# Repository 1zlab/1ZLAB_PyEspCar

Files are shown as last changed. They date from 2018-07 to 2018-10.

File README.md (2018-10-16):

# PyEspCar - 基于MicroPython-ESP32的WIFI小车

**1Z实验室出品**
**1ZLAB**： **Make Things Easy**

## 项目简介

1ZLab在准备挑选合适的小车来研发计算机视觉的教程时候 , 发现习惯了Python语法的我们, 在市面上找不到合适小车, 后来我们选了ESP32作为小车的控制主板, 可以使用Python对其进行交互式编程, 极大的提升了开发效率.

下图是我们的**PyESPCar V2.1**版本的实物图, 舵机云台上面挂载了手机, 可以通过手机WIFI传图, 然后在PC上用OpenCV做图像处理, 然后PC发送控制指令给PyESPCar WIFI小车. 

## 购买PyESPCar

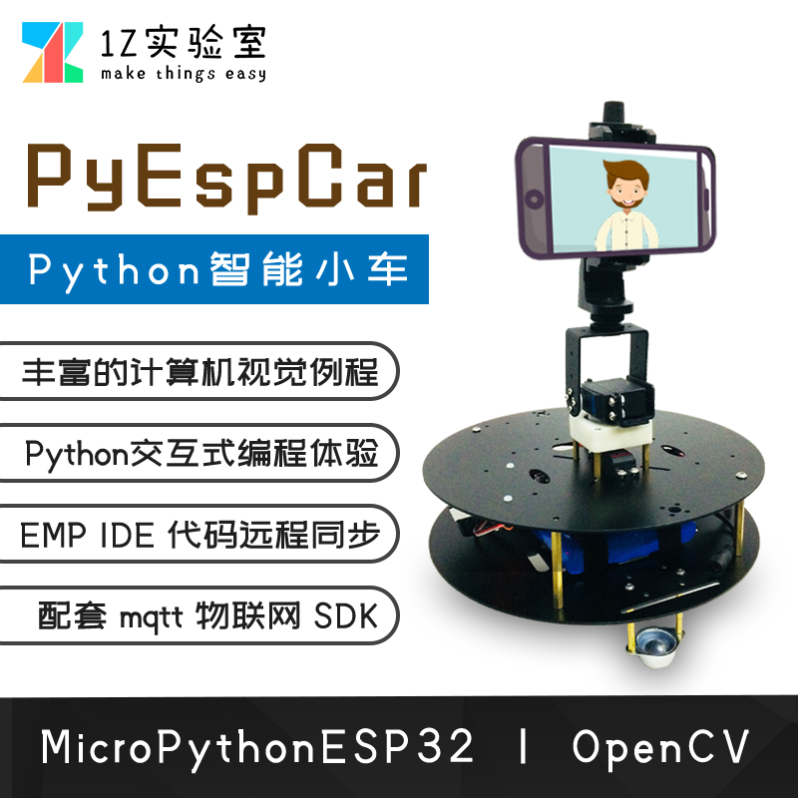
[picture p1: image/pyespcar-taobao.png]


[淘宝-PyESPCar购买链接](https://item.taobao.com/item.htm?id=579247648473)

## 小车自身特性

* MicroPython编程，小车通过repl交互式编程

* **远程调试**，通过WebREPL，可以远程给小车进行编程，上传/同步代码文件。

* 软件硬件与机械结构全部**开源(Open Source)**。

  不用购买之后再提供，直接放在Github上，后续再配套教程持续制作用户友好的**文档**

* **配套教程**  制作PyEspCar Z1的视频教程（讲micropython-esp32与运动控制），发布在**Bilibili**上面， 内容可以参考下文的 `MicroPython-ESP32教学`与 `自控与运动学控制` 这两部分。

  B站主页： https://space.bilibili.com/40344504/#/

* **代码规范**，逐行注释，容易看懂， 参见代码仓库。

* 自主研发**ESP32 Web IDE**， [IDE地址](http://dev.1zlab.com)

## 开发文档

* [PyESPCar开发环境配置](./doc/PyESPCar%E5%BC%80%E5%8F%91%E7%8E%AF%E5%A2%83%E9%85%8D%E7%BD%AE_pyespcar-environment-config/PyESPCar%E5%BC%80%E5%8F%91%E7%8E%AF%E5%A2%83%E9%85%8D%E7%BD%AE_pyespcar-environment-config.md)
## 综合例程

[PyESPCar按键控制模式](https://github.com/1zlab/1ZLAB_PyEspCar/tree/master/examples/01-keyboards_ctl_mode)

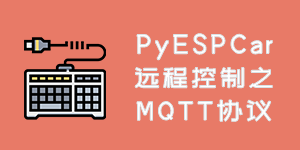
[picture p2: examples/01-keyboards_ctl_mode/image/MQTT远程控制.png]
mqtt keyboards


[PyESPCar色块追踪](https://github.com/1zlab/1ZLAB_PyEspCar/tree/master/examples/02-color-block-track)

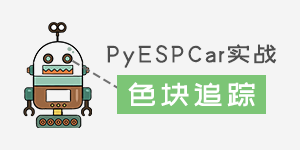
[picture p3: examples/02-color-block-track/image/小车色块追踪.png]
color track


## 机械结构与硬件

* **轻量级二自由度云台**

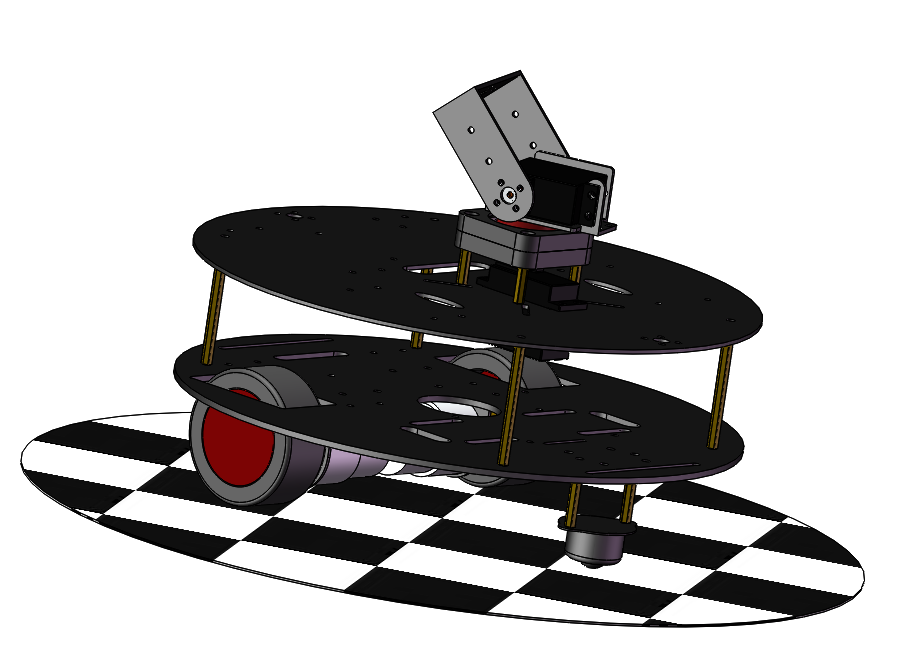
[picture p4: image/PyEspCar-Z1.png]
machine
  

  更适合放在小车上面，同时末端可以承受较大负载（例如手机）。

  高品质20KG 数字舵机， 后期可以拓展为机械臂。

* **PyESPCar 小车底板** 

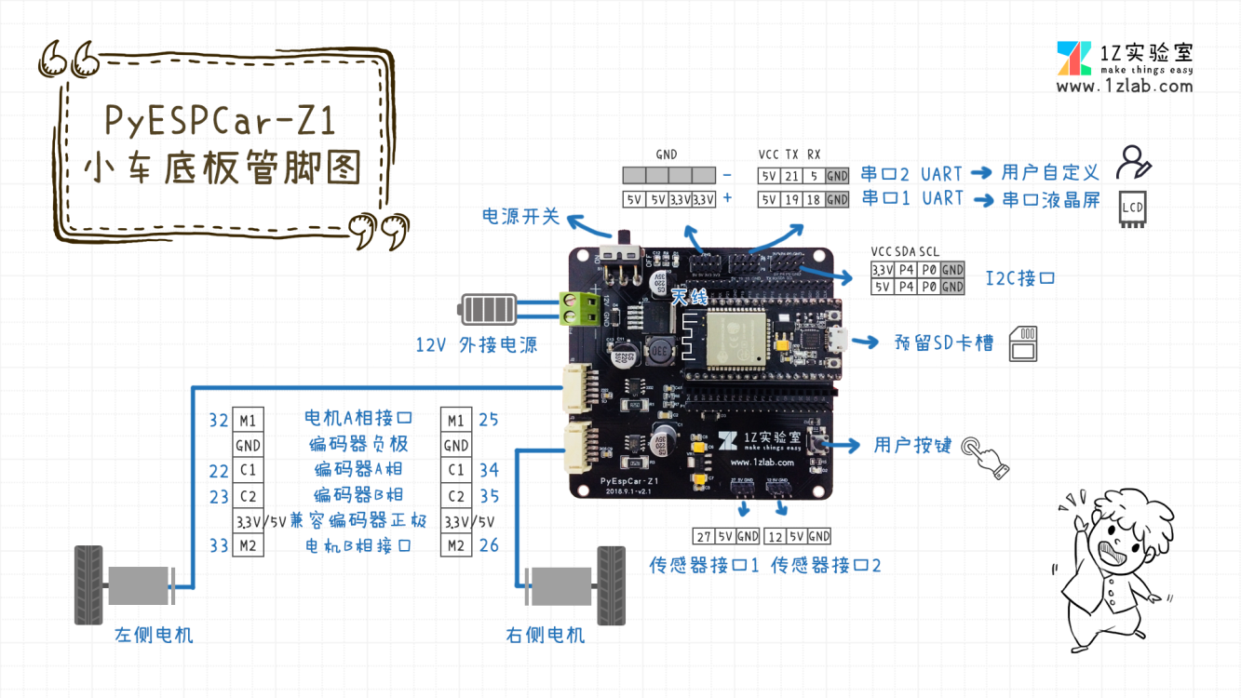
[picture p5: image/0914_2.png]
  

  填补了目前ESP32小车底板的空白，主控采用安信可公司的NodeMCU32s，直插在小车底板上。

  板子预留资源如下: 

  *  用户按键 ×1
  *  电机与AB相编码器接口 ×2
   *  传感器接口×2  
   *  UART串口x2  
   *  I2C接口 x1（两个I2C插口）

* **全金属双层小车底板**  材质选用铝合金，比亚克力更坚固， 尺寸比一般的两轮差速小车大270mm。

  底板上面也预留了**数莓派**，二自由度云台，电池，超声波，ESP32小车控制板,还有**激光雷达**的孔位。

* **12V电池组，电池容量6000毫安时**， 配套充电器

## 贡献者(Ccontributor)

**特别感谢魏彦峰同学在机械结构设计还有小车控制板设计做出的贡献。**

* [魏彦峰-1Z实验室&中国地质大学（武汉）](https://github.com/rose-w)
* [邢顺凯-1Z实验室&杭州电子科技大学](https://github.com/mushroom-x)
* [吴彬聪-1Z实验室&杭州电子科技大学](https://github.com/littleoniononion)
* [刘新宇-廊坊师范](https://github.com/LiuXinyu12378)
* [杨子豪-平衡小车之家](http://minibalance.com/)

## 加入1Z实验室

出品：1Z实验室 （1ZLAB： Make Things Easy）

1Z实验室 Make Things Easy . 致力于在机器人+计算机视觉+人工智能的重叠区域, 制作小白友好的教程.
1zlab

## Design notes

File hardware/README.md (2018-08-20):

# ESP32小车硬件开源文件

## ESP32小车控制板

> TODO 焊接完成之后贴图

## 小车底盘机械结构

>注:所有建模均使用 SolidWorks2016 创建.

* [车身部分](#车身部分)
* [动力部分](#动力部分)
* [云台部分](#云台部分)

### 车身部分

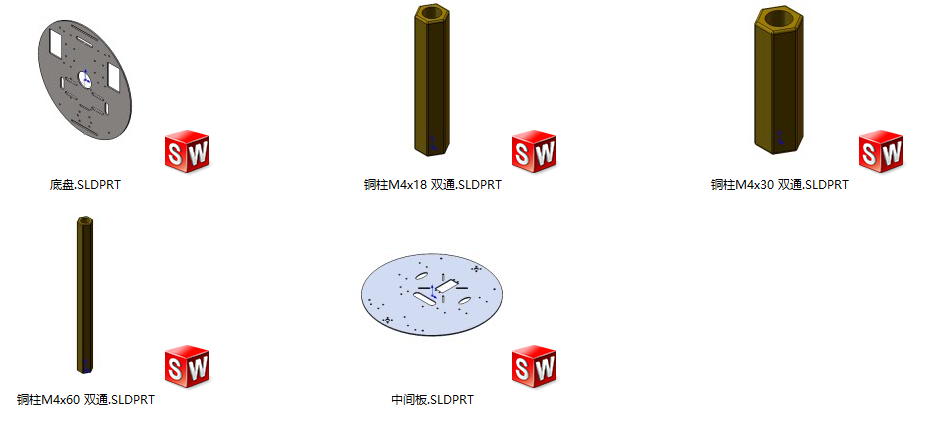
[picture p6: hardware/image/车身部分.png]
车身部分


底盘金属加工图纸

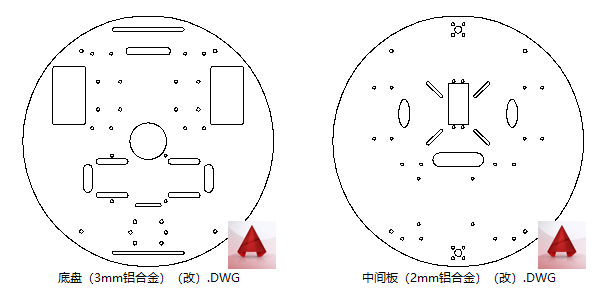
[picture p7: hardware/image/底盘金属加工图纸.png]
底盘金属加工图纸


### 动力部分

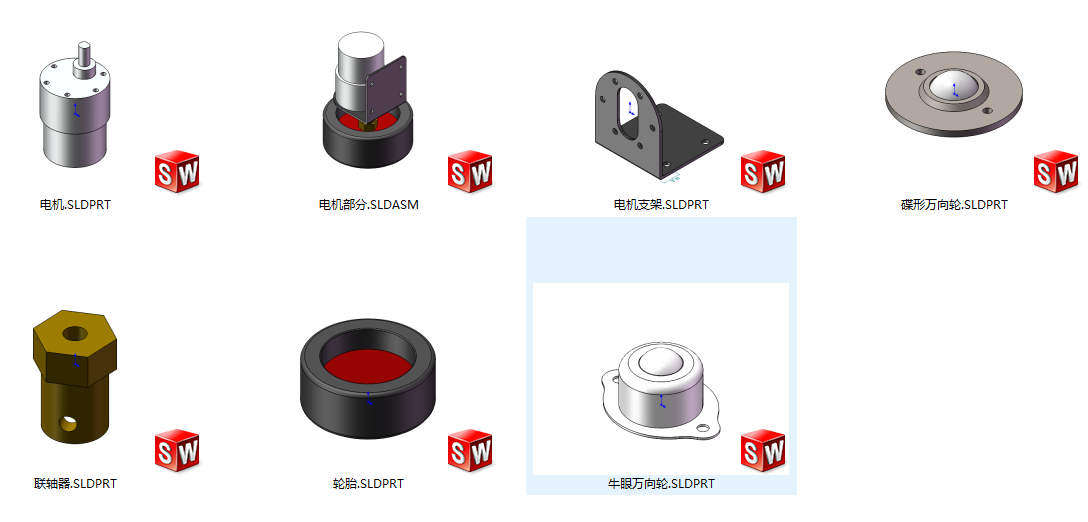
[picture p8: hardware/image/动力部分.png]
动力部分


### 云台部分

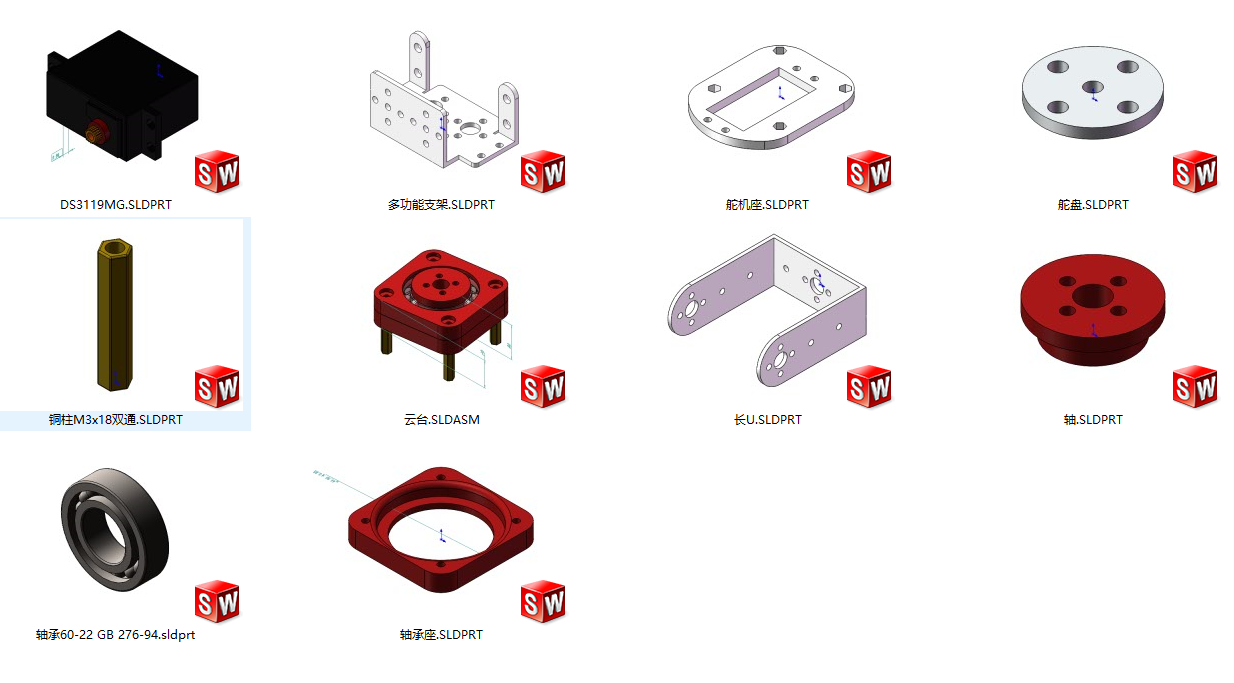
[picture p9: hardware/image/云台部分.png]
云台部分


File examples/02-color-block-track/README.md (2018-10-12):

# PyESPCar色块追踪

## 简介

pyespcar tracker

使用PyESPCar还有OpenCV实现色块追踪, OpenCV识别色块,然后计算偏移量,通过MQTT协议发送给PyESPCar小车. 源码见:https://github.com/1zlab/1ZLAB_PyEspCar/tree/master/examples/02-color-block-track

## 效果演示

效果视频已上传至B站:

[PyESPCar色块追踪效果演示-1Z实验室](https://www.bilibili.com/video/av33370828)

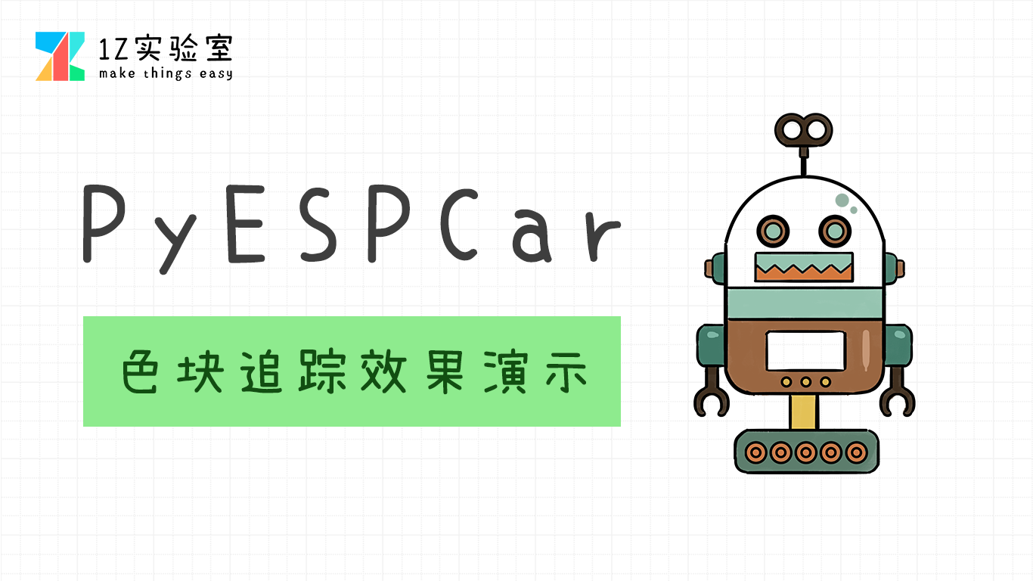
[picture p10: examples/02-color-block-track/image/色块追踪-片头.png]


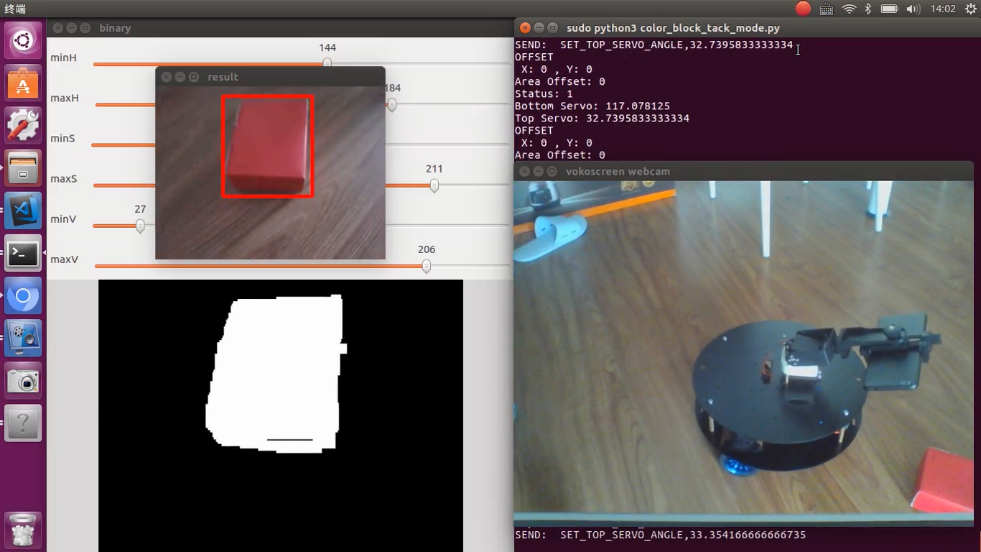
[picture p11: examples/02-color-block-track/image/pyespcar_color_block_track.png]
color block


使用教程与操作流程见`src/README.md`

教程已上传至1zlab.com
[PyESPCar色块追踪小车-主题课程](http://www.1zlab.com/book/opencv-color-track-car-pyespcar/)

加群参与讨论
ad

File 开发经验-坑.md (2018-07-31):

# 存在问题

## 关于ADC的问题

- Invalid Pin for ADC
TODO 查阅文档 需要修改固件 (成本比较高, 而且浪费资源)
IO2 -> ADC2 Channel 2
TODO 改固件 从而可以支持ADC2
临时方案 底板Uno(A0) - 接Uno(A2) = ESP32 GPIO35
BUG 电压取值adc采样 不稳 一直在浮动 

多次采样然后平均
与标准电压比对 (5v 3v) * 系数

## [已解决] IRQ外部中断

MicroPython-ESP32中, irq 只有上升沿或下降沿 (二选1)

>TODO 修改固件, 添加Change模式. 

**而且这里需要的应该是-非阻塞(no-blocking)模式**

**查看ESP-IDF是否有这个API**
是否有必要使用外部中断, 可以使用定时器, 定时查看IO电平是否变化
https://github.com/BramRausch/encoderLib

ESP32 是否有硬件计数?

## [已解决]增量式编码器使用
编码器噪声问题 不是完全按照 0132的顺序来的。

两个引脚都是中断。

TODO 寻找项目参考
添加滤波器

1. 比对 可以大于等于两个？
2. 二者相等的情景？ 
3. 添加状态机 State (之前一直在正转 马上反转的可能性不大。)
4. 是否引入变量： 触发中断的管脚

**增量式编码器**
https://blog.csdn.net/cuhkljt/article/details/25845217
https://item.taobao.com/item.htm?spm=a230r.1.14.27.63de2886VbW8iL&id=45347924687&ns=1&abbucket=6#detail

**ESP32的IRQ是软件中断，相应速度不够， 改用定时器问题就解决了**

## 刷固件

刷固件， 需要把ESP32开发板从底板下取下。
> 有时需要有时不需要

## 声明引脚输入输出是个好习惯
Pin.IN
Pin.OUT

## [Done]电机引脚问题

Problem 左侧电机一动，reboot -> 更换引脚已解决 （因为用了D2接口）

## [Done]电机只能反转不能正转？
电机驱动模块插反
**电机驱动模块有正反**

## Flash损坏，不稳定

ERRORS
----main.py文件损毁？---
rst:0x1 (POWERON_RESET),boot:0x33 (SPI_FAST_FLASH_BOOT)
flash read err, 1000
ets_main.c 371 
ets Jun  8 2016 00:22:57

## [Done 1/2]定时器中断-连不上 传不了文件

main.py里面设定了定时器中断，导致不能通过ampy传文件，只能重置固件。

**ESP32的固件存放在RAM， 文件系统放置在ROM里面, 也就是说，重新刷固件并不会修改文件系统中的代码。**

如果程序里面一直在循环while True，repl资源一直被占用，无法写入程序。
所以需要链接repl，然后将main.py写为空，reboot一下，就解决了。

```python
f = open('main.py', 'w')
f.write('')
f.save
```

在`main.py`里面如果是定时器，定时器一直Print， 这个是个 **死结**
> 这种情况要如何处理？

这个问题可以预防，设置一个外部按键, 然后将main.py清空  write('')
> 修改固件 修改boot.py (留一手)

## 重置MicroPython-ESP32的文件系统

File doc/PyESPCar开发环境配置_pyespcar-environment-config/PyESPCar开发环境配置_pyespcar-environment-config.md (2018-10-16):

# PyESPCar开发环境配置

## 写在前面

自己配置Ubuntu开发环境略麻烦, 后续1Z实验室会提供配置好的虚拟机给大家.

## 为什么用Ubuntu?

我们的PyESPCar开发教程以及OpenCV图像处理部分的教程都是在Ubuntu下进行的, 因为Ubuntu下开发环境更加友好.  同时针对**VIP**用户, 我们还提供Ubuntu远程协助的服务.

Ubuntu是你步入开源世界的大门. 你可以选择在虚拟机下安装Ubuntu, 也可以选择在真机上安装Ubuntu.

在Ubuntu下,  我们的工程使用Python一统天下, Python完成嵌入式开发,机器人控制, Python进行图像处理, Python进行物联网通信. 所以你只需要精通这一门语言就足够了.

## Ubuntu下的开发环境配置

为了大家方便, 这里我还是把Ubuntu所需配置的环境在这里讲一下, 做一下汇总.

### Ubuntu虚拟机安装

如果你是用的Ubuntu虚拟机的话, 1Z实验室有虚拟机的安装教程:

[Ubuntu虚拟机安装-VirtualBox](https://github.com/1zlab/1ZLAB_OpenCV_Tutorial/blob/master/%E9%99%84%E5%BD%95A.OpenCV%E5%BC%80%E5%8F%91%E7%8E%AF%E5%A2%83%E9%85%8D%E7%BD%AE/Ubuntu/1.Ubuntu%E8%99%9A%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)

### Git

git是工程版本管理工具, 你可以使用Git从Github克隆PyESPCar的开源工程.

在Ubuntu上安装git:

```bash
sudo apt-get install git
```

### pip3

Ubuntu16.04自带的默认Python版本是python3.5, 需要安装`pip3` 作为python的包管理工具. 

```bash
sudo apt-get install python3-pip
```

### Python科学计算工具包

做科学计算需要安装下面的一些工具包

```bash
sudo pip3 install jupyter ipython numpy scipy matplotlib
```

### 安装OpenCV

非官方的OpenCV预编译的包.
同时安装opencv的main还有contrib部分.

```bash
pip install opencv-contrib-python
```

详情见文档:
[opencv-python 3.4.3.18](https://pypi.org/project/opencv-python/)

### PyGame

PyGame是用于写游戏的.

因为我们用到了PyGame的键盘事件监听, 所以需要安装这个包.

```bash
sudo pip3 install pygame
```

### MicroPython-ESP32开发环境配置

PyESPCar是基于MicroPython-ESP32的, 所以MicroPython-ESP32的基本操作, 是需要你自己去学习的.

完整的教程见1Z实验室出品的: [MicroPython-ESP32从入门到差不多](https://github.com/1zlab/1ZLAB_MicroPython_ESP32_Tutorial)

下面的教程是你玩PyESPCar必须要看的.

- [MicroPython-ESP32固件烧录](https://github.com/1zlab/1ZLAB_MicroPython_ESP32_Tutorial/blob/master/01_MicroPython-ESP32%E5%9B%BA%E4%BB%B6%E7%83%A7%E5%BD%95/MicroPython-ESP32%E5%9B%BA%E4%BB%B6%E7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)
- [ESP32的REPL使用方法](https://github.com/1zlab/1ZLAB_MicroPython_ESP32_Tutorial/blob/master/02_ESP32%E7%9A%84REPL%E4%BD%BF%E7%94%A8%E6%96%B9%E6%B3%95/ESP32%E7%9A%84REPL%E4%BD%BF%E7%94%A8%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)
- [ESP32接入WIFI热点](https://github.com/1zlab/1ZLAB_MicroPython_ESP32_Tutorial/blob/master/17_ESP32%E6%8E%A5%E5%85%A5WIFI%E7%83%AD%E7%82%B9/ESP32%E6%8E%A5%E5%85%A5WIFI%E7%83%AD%E7%82%B9.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)
- [使用upip安装包](https://github.com/1zlab/1ZLAB_MicroPython_ESP32_Tutorial/blob/master/16_%E4%BD%BF%E7%94%A8upip%E5%AE%89%E8%A3%85%E5%8C%85/%E4%BD%BF%E7%94%A8upip%E5%AE%89%E8%A3%85%E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)
- [WebREPL与MIcroIDE配置教程](https://github.com/1zlab/1ZLAB_MicroPython_ESP32_Tutorial/blob/master/14_WebREPL%E4%B8%8EMIcroIDE%E9%85%8D%E7%BD%AE%E6%95%99%E7%A8%8B/WebREPL%E4%B8%8EMIcroIDE%E9%85%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)
- [利用AMPY进行文件同步](https://github.com/1zlab/1ZLAB_MicroPython_ESP32_Tutorial/blob/master/18_%E5%88%A9%E7%94%A8AMPY%E8%BF%9B%E8%A1%8C%E6%96%87%E4%BB%B6%E5%90%8C%E6%AD%A5/%E5%88%A9%E7%94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)
- [MQTT入门之概念解析](https://github.com/1zlab/1ZLAB_MicroPython_ESP32_Tutorial/blob/master/15_MQTT%E5%85%A5%E9%97%A8%E4%B9%8B%E6%A6%82%E5%BF%B5%E8%A7%A3%E6%9E%90/MQTT%E5%85%A5%E9%97%A8%E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)
- [MQTT入门之项目实战](https://github.com/1zlab/1ZLAB_MicroPython_ESP32_Tutorial/blob/master/19_MQTT%E5%85%A5%E9%97%A8%E4%B9%8B%E9%A1%B9%E7%9B%AE%E5%AE%9E%E6%88%98/MQTT%E5%85%A5%E9%97%A8%E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)

下方做了一下汇总:

一个是固件烧录, 你需要安装`esptool`

```bash
sudo pip3 install esptool --upgrade
```

详情见: [MicroPython-ESP32固件烧录](https://github.com/1zlab/1ZLAB_MicroPython_ESP32_Tutorial/blob/master/01_MicroPython-ESP32%E5%9B%BA%E4%BB%B6%E7%83%A7%E5%BD%95/MicroPython-ESP32%E5%9B%BA%E4%BB%B6%E7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)

通过REPL与MicroPython-ESP32交互, 你需要使用`picocom`

```bash
sudo apt-get install picocom
```

详情见: [ESP32的REPL使用方法](https://github.com/1zlab/1ZLAB_MicroPython_ESP32_Tutorial/blob/master/02_ESP32%E7%9A%84REPL%E4%BD%BF%E7%94%A8%E6%96%B9%E6%B3%95/ESP32%E7%9A%84REPL%E4%BD%BF%E7%94%A8%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)

通过AMPY进行文件同步, 需要安装AMPY

```bash
sudo pip3 install adafruit-ampy --upgrade
```

详情见: [利用AMPY进行文件同步](https://github.com/1zlab/1ZLAB_MicroPython_ESP32_Tutorial/blob/master/18_%E5%88%A9%E7%94%A8AMPY%E8%BF%9B%E8%A1%8C%E6%96%87%E4%BB%B6%E5%90%8C%E6%AD%A5/%E5%88%A9%E7%94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)

MQTT相关的, 需要安装**mosquitto**

```bash
sudo apt-get install mosquitto mosquitto-clients 
```

使用pip3 安装`paho-mqtt`

```bash
sudo pip3 install paho-mqtt
```

详情见: [MQTT入门之项目实战](https://github.com/1zlab/1ZLAB_MicroPython_ESP32_Tutorial/blob/master/19_MQTT%E5%85%A5%E9%97%A8%E4%B9%8B%E9%A1%B9%E7%9B%AE%E5%AE%9E%E6%88%98/MQTT%E5%85%A5%E9%97%A8%E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)

## PyESPCar的工程文件介绍

PyESPCar的工程文件见:

[https://github.com/1zlab/1ZLAB_PyEspCar](https://github.com/1zlab/1ZLAB_PyEspCar)

使用git将这个文件夹clone克隆到本地文件夹.

> 对git不熟悉的同学, 需要自学一下git相关的操作.

```bash
git clone https://github.com/1zlab/1ZLAB_PyEspCar.git
```

这里主要讲一下工程里面源码的分布:

`src/esp32` 里面是micropython-esp32相关的代码.

`src/pc` 上面的代码是在PC上运行的.

```bash
➜  src git:(master) ✗ tree
.
├── esp32
│   ├── battery_voltage.py
│   ├── button.py
│   ├── car_config.py
│   ├── car.py
│   ├── cloud_platform.py
│   ├── led.py
│   ├── main.py
│   ├── motor.py
│   ├── mqtt_control_mode.py
│   ├── pca9685.py
│   ├── test_car.py
│   ├── test_motor.py
│   └── user_button.py
└── pc
    ├── car_config.py
    ├── pyespcar_sdk.py
    ├── README.md
    └── test_pyespcar_sdk.py

```

## 修改IP地址

需要修改`src/esp32/mqtt_control_mode.py` 的源码.

这里的`SERVER` 是我本机(Ubuntu)的IP地址.

```python
SERVER = '192.168.43.16'
CLIENT_ID = 'PYESPCAR_A0'
MQTT_TOPIC_ID = b'PYESPCAR_CTL_MSG'
```

如何查看PC在局域网的IP地址? 在bash里面输入:

```bash
ifconfig
```

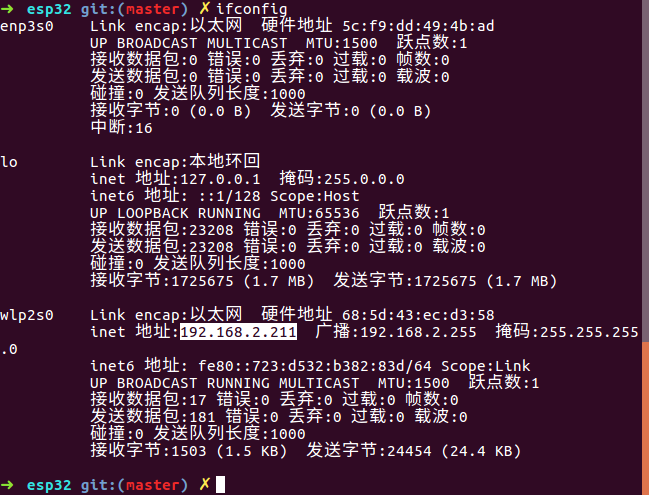
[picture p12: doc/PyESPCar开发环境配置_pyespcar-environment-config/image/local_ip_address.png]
local ip address


其中的`inet 地址:192.168.2.211` 就是我们的本地地址.

局域网下每个设备的IP地址都是不一样的.

**注意 SERVER是Ubuntu的IP地址, 不是ESP32的IP地址**

**注意 SERVER是Ubuntu的IP地址, 不是ESP32的IP地址**

**注意 SERVER是Ubuntu的IP地址, 不是ESP32的IP地址**

## 虚拟机设置网络桥接

> 如果你用的是真机可以跳过这个步骤.

另外如果你使用是虚拟机, 默认一般是NAT网络, 局域网下的设备访问不了虚拟机, 主机也访问不了虚拟机. 

首先需要把当前的虚拟机关闭.

在虚拟机的设置选项, 点击网络, 需要把网络设置为**桥接模式**. 设置完成之后, 重启虚拟机. Virtualbox默认是自动配置完成, 局域网IP分配默认会设置为 DHCP. 

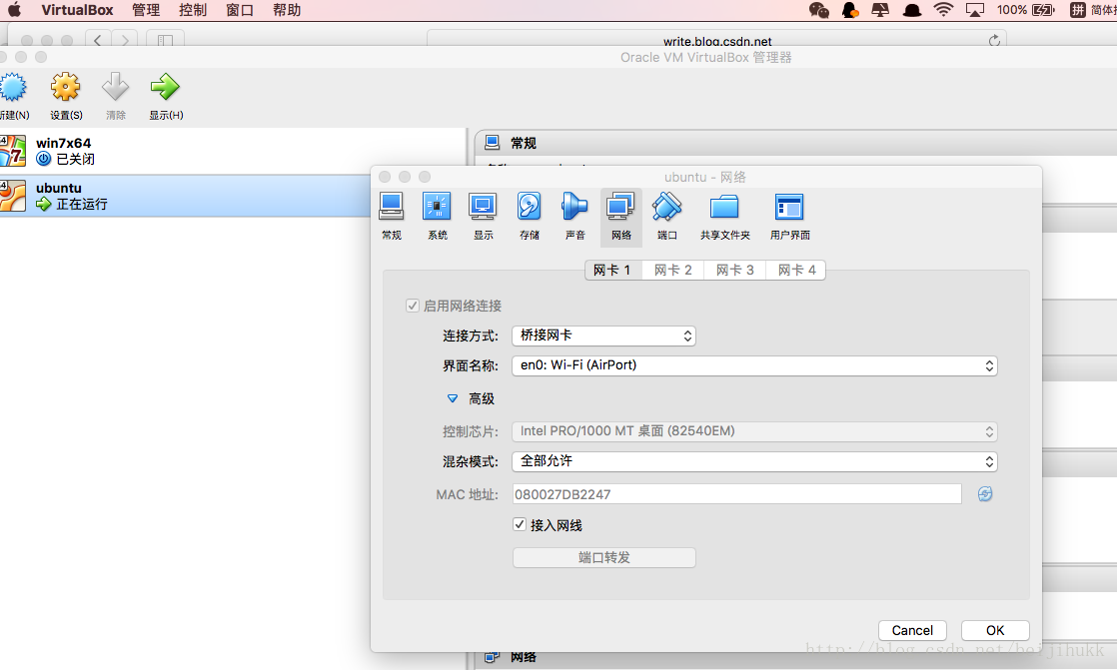
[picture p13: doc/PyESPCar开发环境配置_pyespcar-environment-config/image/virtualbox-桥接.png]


在Ubuntu虚拟机里面执行`ifconfig`  查看更新后的IP地址.

> 后面的操作假定,你的Host主机是Windows.

查看你的Host主机跟虚拟机的IP前缀是否一样, 例如 Host是`192.168.2.4` , 虚拟机的IP是`192.168.2.221`,  他们的前缀都是**192.168.43** , 所以是在一个局域网下. 

假如你的Host主机是Windows的, 打开Windows的CMD, 输入命令行, 查看IP

```bash
ipconfig
```

然后看在主机能不能ping通虚拟机:

```
ping 192.168.2.221
```

如果可以ping通, 就可以进行下一步的配置.

## 上传代码到ESP32开发板

克隆下来之后`src` 文件夹下是所有的`PyESPCar`的源码. 其中`src/esp32` 文件夹下的文件是需要上传到ESP32开发板的. 

> 1Z实验室后续发货的开发板(带核心板)的版本已经帮大家上传好了所需的文件. 但是src/esp32/mqtt_control_mode.py 还是需要你自己再传一下.

那用什么方式传文件呢?  

1. 你可以选择使用1Z实验室的EMP IDE, 在Web上面把文件一个个传上去. 
2. 可以使用AMPY, 通过命令行的方式一个一个将文件传进去. 
3. 另外阿凯也写了一个批量上传的脚本, [update-all](https://github.com/1zlab/1ZLAB_PyEspCar/blob/master/tools/update_all.py) . 通过ampy上传当前目录下的所有文件.

**自我检查, 文件名命名, 内容有没有粘贴错误!!!!**

## 打开PyESPCar的电源开关

打开PyESPCar电源开关, 电源指示灯会亮.

**这一步很重要!!!**

## 关闭WebREPL模式

WebREPL模式会跟MQTT通信**资源抢占**, 导致网络不稳定.

 `main.py` 里面默认上电运行的是mqtt模式, 所以我们需要把webrepl模式关掉.

> 注: webrepl模式关掉, 也就意味着关掉后不能与EMP IDE进行连接.

设置boot启动模式为`1` **boot with wifi startup**

```python
>>> import emp_boot
>>> emp_boot.set_boot_mode()
```

填入数字`1`,  

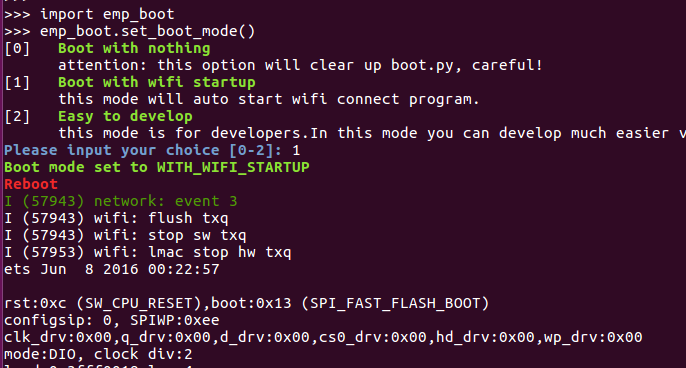
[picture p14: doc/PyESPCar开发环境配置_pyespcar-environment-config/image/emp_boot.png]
emp_boot


完成配置.

## 阶段自我检查

在执行下一步之前, 确保你已经:

1. 通过picocom连接到ESP32开发板的REPL:  [ESP32的REPL使用方法](https://github.com/1zlab/1ZLAB_MicroPython_ESP32_Tutorial/blob/master/02_ESP32%E7%9A%84REPL%E4%BD%BF%E7%94%A8%E6%96%B9%E6%B3%95/ESP32%E7%9A%84REPL%E4%BD%BF%E7%94%A8%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)
2. 按照教程里面的说明, 连接上了WIFI热点: [ESP32接入WIFI热点 ](https://github.com/1zlab/1ZLAB_MicroPython_ESP32_Tutorial/blob/master/17_ESP32%E6%8E%A5%E5%85%A5WIFI%E7%83%AD%E7%82%B9/ESP32%E6%8E%A5%E5%85%A5WIFI%E7%83%AD%E7%82%B9.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), PC与ESP32连入同一个局域网.
3. 通过upip安装了`emp-1zlab`  与`umqtt.simple`  [使用upip安装包](https://github.com/1zlab/1ZLAB_MicroPython_ESP32_Tutorial/blob/master/16_%E4%BD%BF%E7%94%A8upip%E5%AE%89%E8%A3%85%E5%8C%85/%E4%BD%BF%E7%94%A8upip%E5%AE%89%E8%A3%85%E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) ,  [MQTT入门之项目实战](https://github.com/1zlab/1ZLAB_MicroPython_ESP32_Tutorial/blob/master/19_MQTT%E5%85%A5%E9%97%A8%E4%B9%8B%E9%A1%B9%E7%9B%AE%E5%AE%9E%E6%88%98/MQTT%E5%85%A5%E9%97%A8%E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)
4. 将PyESPCar的工程文件, 传入到了ESP32的文件系统中.
5. 关闭esp32的webrepl模式
6. 打开PyESPCar的**电源开关**
7. 按下开发板上的**reset按钮**, 重启后自动进入MQTT远程控制模式.

## 测试PyESPCarSDK

> 首先确保PyESPCar进入了MQTT模式, 成功连入局域网.

`src/pc` 下面是PyESPCar SDK 的源码还有简单的测试.

首先我们要进入到`src/pc` 所在的目录下.

然后执行`ipython` , 进入交互式命令行模式.

输入以下内容, 执行测试pyespcar sdk的测试程序.

```python
exec(open('test_pyespcar_sdk.py').read(), globals())
```

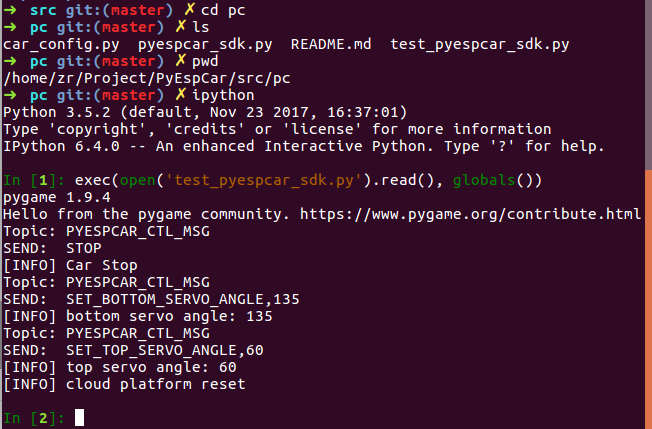
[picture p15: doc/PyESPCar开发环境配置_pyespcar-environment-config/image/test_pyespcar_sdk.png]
pyespcar


然后你就可以调用`sdk`的各种方法, 进行测试.

例如调用`turn_left` 方法, 让小车左转.

```python
>>> sdk.turn_left()
Topic: PYESPCAR_CTL_MSG
SEND:  TURN_LEFT,60
[INFO] car turn left, speed: 60, delay_ms: None

```

调用`turn_right`方法, 让小车右转.

```python
>>> sdk.turn_right()
Topic: PYESPCAR_CTL_MSG
SEND:  TURN_RIGHT,60
[INFO] car turn right, speed: 60, delay_ms: None

```

详情见`src/pc/pyespcar_sdk.py`

## 综合项目

`examples`下是目前所有的PyESPCar的样例代码.

[PyESPCar按键控制模式](https://github.com/1zlab/1ZLAB_PyEspCar/tree/master/examples/01-keyboards_ctl_mode)

mqtt keyboards

[PyESPCar色块追踪](https://github.com/1zlab/1ZLAB_PyEspCar/tree/master/examples/02-color-block-track)

color track 

 [PyESPCar色块追踪小车-主题课程](http://www.1zlab.com/topic/opencv-color-track-car-pyespcar/)

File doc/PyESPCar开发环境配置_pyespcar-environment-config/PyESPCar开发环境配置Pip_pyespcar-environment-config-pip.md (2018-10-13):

# PyESPCar开发环境配置

## 写在前面

我们的PyESPCar开发教程以及OpenCV图像处理部分的教程都是在Ubuntu下进行的, 因为Ubuntu下开发环境更加友好.  同时针对**VIP**用户, 我们还提供Ubuntu远程协助的服务.

Ubuntu是你步入开源世界的大门. 你可以选择在虚拟机下安装Ubuntu, 也可以选择在真机上安装Ubuntu.

在Ubuntu下,  我们的工程使用Python一统天下, Python完成嵌入式开发,机器人控制, Python进行图像处理, Python进行物联网通信. 所以你只需要精通这一门语言就足够了.

## Ubuntu下的开发环境配置

为了大家方便, 这里我还是把Ubuntu所需配置的环境在这里讲一下, 做一下汇总.

### Ubuntu虚拟机安装

如果你是用的Ubuntu虚拟机的话, 1Z实验室有虚拟机的安装教程:

[Ubuntu虚拟机安装-VirtualBox](https://github.com/1zlab/1ZLAB_OpenCV_Tutorial/blob/master/%E9%99%84%E5%BD%95A.OpenCV%E5%BC%80%E5%8F%91%E7%8E%AF%E5%A2%83%E9%85%8D%E7%BD%AE/Ubuntu/1.Ubuntu%E8%99%9A%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)

### Git

git是工程版本管理工具, 你可以使用Git从Github克隆PyESPCar的开源工程.

在Ubuntu上安装git:

```bash
sudo apt-get install git
```

### Anaconda

Anaconda是Python的科学计算包. 

[在Ubuntu下安装Anaconda科学计算包](https://github.com/1zlab/1ZLAB_OpenCV_Tutorial/blob/master/%E9%99%84%E5%BD%95A.OpenCV%E5%BC%80%E5%8F%91%E7%8E%AF%E5%A2%83%E9%85%8D%E7%BD%AE/Ubuntu/2.Ubuntu%E5%AE%89%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)

ipython, numpy等等, 这些包, 在安装Anaconda的时候, 也就一同安装好了.

### 安装OpenCV

图像处理方面需要安装**python-opencv**

使用anaconda安装opencv比较简单:

- [通过Anaconda安装OpenCV](https://github.com/1zlab/1ZLAB_OpenCV_Tutorial/blob/master/%E9%99%84%E5%BD%95A.OpenCV%E5%BC%80%E5%8F%91%E7%8E%AF%E5%A2%83%E9%85%8D%E7%BD%AE/Ubuntu/3.%E9%80%9A%E8%BF%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)

更多OpenCV教程见 [1zlab.com](1zlab.com)

教程里面有从源码编译并安装OpenCV的教程, 但是不建议小白尝试. 但是对于数莓派用户来说, Anaconda是不可以用的, OpenCV也只能从源码编译.

### PyGame

PyGame是用于写游戏的.

因为我们用到了PyGame的键盘事件监听, 所以需要安装这个包.

```bash
sudo pip3 install pygame
```

### MicroPython-ESP32开发环境配置

PyESPCar是基于MicroPython-ESP32的, 所以MicroPython-ESP32的基本操作, 是需要你自己去学习的.

完整的教程见1Z实验室出品的: [MicroPython-ESP32从入门到差不多](https://github.com/1zlab/1ZLAB_MicroPython_ESP32_Tutorial)

下面的教程是你玩PyESPCar必须要看的.

- [MicroPython-ESP32固件烧录](https://github.com/1zlab/1ZLAB_MicroPython_ESP32_Tutorial/blob/master/01_MicroPython-ESP32%E5%9B%BA%E4%BB%B6%E7%83%A7%E5%BD%95/MicroPython-ESP32%E5%9B%BA%E4%BB%B6%E7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)
- [ESP32的REPL使用方法](https://github.com/1zlab/1ZLAB_MicroPython_ESP32_Tutorial/blob/master/02_ESP32%E7%9A%84REPL%E4%BD%BF%E7%94%A8%E6%96%B9%E6%B3%95/ESP32%E7%9A%84REPL%E4%BD%BF%E7%94%A8%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)
- [ESP32接入WIFI热点](https://github.com/1zlab/1ZLAB_MicroPython_ESP32_Tutorial/blob/master/17_ESP32%E6%8E%A5%E5%85%A5WIFI%E7%83%AD%E7%82%B9/ESP32%E6%8E%A5%E5%85%A5WIFI%E7%83%AD%E7%82%B9.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)
- [使用upip安装包](https://github.com/1zlab/1ZLAB_MicroPython_ESP32_Tutorial/blob/master/16_%E4%BD%BF%E7%94%A8upip%E5%AE%89%E8%A3%85%E5%8C%85/%E4%BD%BF%E7%94%A8upip%E5%AE%89%E8%A3%85%E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)
- [WebREPL与MIcroIDE配置教程](https://github.com/1zlab/1ZLAB_MicroPython_ESP32_Tutorial/blob/master/14_WebREPL%E4%B8%8EMIcroIDE%E9%85%8D%E7%BD%AE%E6%95%99%E7%A8%8B/WebREPL%E4%B8%8EMIcroIDE%E9%85%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)
- [利用AMPY进行文件同步](https://github.com/1zlab/1ZLAB_MicroPython_ESP32_Tutorial/blob/master/18_%E5%88%A9%E7%94%A8AMPY%E8%BF%9B%E8%A1%8C%E6%96%87%E4%BB%B6%E5%90%8C%E6%AD%A5/%E5%88%A9%E7%94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)
- [MQTT入门之概念解析](https://github.com/1zlab/1ZLAB_MicroPython_ESP32_Tutorial/blob/master/15_MQTT%E5%85%A5%E9%97%A8%E4%B9%8B%E6%A6%82%E5%BF%B5%E8%A7%A3%E6%9E%90/MQTT%E5%85%A5%E9%97%A8%E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)
- [MQTT入门之项目实战](https://github.com/1zlab/1ZLAB_MicroPython_ESP32_Tutorial/blob/master/19_MQTT%E5%85%A5%E9%97%A8%E4%B9%8B%E9%A1%B9%E7%9B%AE%E5%AE%9E%E6%88%98/MQTT%E5%85%A5%E9%97%A8%E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)

下方做了一下汇总:

一个是固件烧录, 你需要安装`esptool`

```bash
sudo pip3 install esptool --upgrade
```

详情见: [MicroPython-ESP32固件烧录](https://github.com/1zlab/1ZLAB_MicroPython_ESP32_Tutorial/blob/master/01_MicroPython-ESP32%E5%9B%BA%E4%BB%B6%E7%83%A7%E5%BD%95/MicroPython-ESP32%E5%9B%BA%E4%BB%B6%E7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)

通过REPL与MicroPython-ESP32交互, 你需要使用`picocom`

```bash
sudo apt-get install picocom
```

详情见: [ESP32的REPL使用方法](https://github.com/1zlab/1ZLAB_MicroPython_ESP32_Tutorial/blob/master/02_ESP32%E7%9A%84REPL%E4%BD%BF%E7%94%A8%E6%96%B9%E6%B3%95/ESP32%E7%9A%84REPL%E4%BD%BF%E7%94%A8%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)

通过AMPY进行文件同步, 需要安装AMPY

```bash
sudo pip install adafruit-ampy --upgrade
```

详情见: [利用AMPY进行文件同步](https://github.com/1zlab/1ZLAB_MicroPython_ESP32_Tutorial/blob/master/18_%E5%88%A9%E7%94%A8AMPY%E8%BF%9B%E8%A1%8C%E6%96%87%E4%BB%B6%E5%90%8C%E6%AD%A5/%E5%88%A9%E7%94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)

MQTT相关的, 需要安装**mosquitto**

```bash
sudo apt-get install mosquitto mosquitto-clients 
```

使用pip3 安装`paho-mqtt`

```bash
sudo pip3 install paho-mqtt
```

详情见: [MQTT入门之项目实战](https://github.com/1zlab/1ZLAB_MicroPython_ESP32_Tutorial/blob/master/19_MQTT%E5%85%A5%E9%97%A8%E4%B9%8B%E9%A1%B9%E7%9B%AE%E5%AE%9E%E6%88%98/MQTT%E5%85%A5%E9%97%A8%E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)

## PyESPCar的工程文件介绍

PyESPCar的工程文件见:

[https://github.com/1zlab/1ZLAB_PyEspCar](https://github.com/1zlab/1ZLAB_PyEspCar)

使用git将这个文件夹clone克隆到本地文件夹.

> 对git不熟悉的同学, 需要自学一下git相关的操作.

```bash
git clone https://github.com/1zlab/1ZLAB_PyEspCar.git
```

这里主要讲一下工程里面源码的分布:

`src/esp32` 里面是micropython-esp32相关的代码.

`src/pc` 上面的代码是在PC上运行的.

```bash
➜  src git:(master) ✗ tree
.
├── esp32
│   ├── battery_voltage.py
│   ├── button.py
│   ├── car_config.py
│   ├── car.py
│   ├── cloud_platform.py
│   ├── led.py
│   ├── main.py
│   ├── motor.py
│   ├── mqtt_control_mode.py
│   ├── pca9685.py
│   ├── test_car.py
│   ├── test_motor.py
│   └── user_button.py
└── pc
    ├── car_config.py
    ├── pyespcar_sdk.py
    ├── README.md
    └── test_pyespcar_sdk.py

```

## 修改IP地址

需要修改`src/esp32/mqtt_control_mode.py` 的源码.

这里的`SERVER` 是我本机(Ubuntu)的IP地址.

```python
SERVER = '192.168.43.16'
CLIENT_ID = 'PYESPCAR_A0'
MQTT_TOPIC_ID = b'PYESPCAR_CTL_MSG'
```

如何查看PC在局域网的IP地址? 在bash里面输入:

```bash
ifconfig
```

local ip address

其中的`inet 地址:192.168.2.211` 就是我们的本地地址.

## 上传代码到ESP32开发板

克隆下来之后`src` 文件夹下是所有的`PyESPCar`的源码. 其中`src/esp32` 文件夹下的文件是需要上传到ESP32开发板的. 

> 1Z实验室后续发货的开发板(带核心板)的版本已经帮大家上传好了所需的文件. 但是src/esp32/mqtt_control_mode.py 还是需要你自己再传一下.

那用什么方式传文件呢?  

1. 你可以选择使用1Z实验室的EMP IDE, 在Web上面把文件一个个传上去. 
2. 可以使用AMPY, 通过命令行的方式一个一个将文件传进去. 
3. 另外阿凯也写了一个批量上传的脚本, [update-all](https://github.com/1zlab/1ZLAB_PyEspCar/blob/master/tools/update_all.py) . 通过ampy上传当前目录下的所有文件.

## 关闭WebREPL模式

WebREPL模式会跟MQTT通信**资源抢占**, 导致网络不稳定.

 `main.py` 里面默认上电运行的是mqtt模式, 所以我们需要把webrepl模式关掉.

> 注: webrepl模式关掉, 也就意味着关掉后不能与EMP IDE进行连接.

设置boot启动模式为`1` **boot with wifi startup**

```python
>>> import emp_boot
>>> emp_boot.set_boot_mode()
```

填入数字`1`,  

emp_boot

完成配置.

## 阶段自我检查

在执行下一步之前, 确保你已经:

1. 通过picocom连接到ESP32开发板的REPL:  [ESP32的REPL使用方法](https://github.com/1zlab/1ZLAB_MicroPython_ESP32_Tutorial/blob/master/02_ESP32%E7%9A%84REPL%E4%BD%BF%E7%94%A8%E6%96%B9%E6%B3%95/ESP32%E7%9A%84REPL%E4%BD%BF%E7%94%A8%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)
2. 按照教程里面的说明, 连接上了WIFI热点: [ESP32接入WIFI热点 ](https://github.com/1zlab/1ZLAB_MicroPython_ESP32_Tutorial/blob/master/17_ESP32%E6%8E%A5%E5%85%A5WIFI%E7%83%AD%E7%82%B9/ESP32%E6%8E%A5%E5%85%A5WIFI%E7%83%AD%E7%82%B9.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), PC与ESP32连入同一个局域网.
3. 通过upip安装了`emp-1zlab`  与`umqtt.simple`  [使用upip安装包](https://github.com/1zlab/1ZLAB_MicroPython_ESP32_Tutorial/blob/master/16_%E4%BD%BF%E7%94%A8upip%E5%AE%89%E8%A3%85%E5%8C%85/%E4%BD%BF%E7%94%A8upip%E5%AE%89%E8%A3%85%E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) ,  [MQTT入门之项目实战](https://github.com/1zlab/1ZLAB_MicroPython_ESP32_Tutorial/blob/master/19_MQTT%E5%85%A5%E9%97%A8%E4%B9%8B%E9%A1%B9%E7%9B%AE%E5%AE%9E%E6%88%98/MQTT%E5%85%A5%E9%97%A8%E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)
4. 将PyESPCar的工程文件, 传入到了ESP32的文件系统中.
5. 关闭esp32的webrepl模式
6. 按下开发板上的reset按钮, 重启后自动进入MQTT远程控制模式.

## 测试PyESPCarSDK

> 首先确保PyESPCar进入了MQTT模式, 成功连入局域网.

`src/pc` 下面是PyESPCar SDK 的源码还有简单的测试.

首先我们要进入到`src/pc` 所在的目录下.

然后执行`ipython` , 进入交互式命令行模式.

输入以下内容, 执行测试pyespcar sdk的测试程序.

```python
exec(open('test_pyespcar_sdk.py').read(), globals())
```

pyespcar

然后你就可以调用`sdk`的各种方法, 进行测试.

例如调用`turn_left` 方法, 让小车左转.

```python
>>> sdk.turn_left()
Topic: PYESPCAR_CTL_MSG
SEND:  TURN_LEFT,60
[INFO] car turn left, speed: 60, delay_ms: None

```

调用`turn_right`方法, 让小车右转.

```python
>>> sdk.turn_right()
Topic: PYESPCAR_CTL_MSG
SEND:  TURN_RIGHT,60
[INFO] car turn right, speed: 60, delay_ms: None

```

详情见`src/pc/pyespcar_sdk.py`

## 综合项目

`examples`下是目前所有的PyESPCar的样例代码.

[PyESPCar按键控制模式](https://github.com/1zlab/1ZLAB_PyEspCar/tree/master/examples/01-keyboards_ctl_mode)

mqtt keyboards

[PyESPCar色块追踪](https://github.com/1zlab/1ZLAB_PyEspCar/tree/master/examples/02-color-block-track)

color track 

 [PyESPCar色块追踪小车-主题课程](http://www.1zlab.com/topic/opencv-color-track-car-pyespcar/)

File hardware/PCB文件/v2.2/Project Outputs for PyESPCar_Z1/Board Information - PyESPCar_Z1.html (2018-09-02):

Altium customize

# Board Information Report

Date: | | 2018/9/1
Time: | | 21:47:44
Elapsed Time: | | 00:00:00
Filename: | | E:\GitHub\1ZLAB_ESP32_WIFI_Car\hardware\PCB文件\v2.1\PyESPCar_Z1.PcbDoc
Units: | | mmmils

## Contents

Contents

Board Specification

General

Routing

Routing Information

Layer Information

Layer Information

Drill Pairs

Board Holes

Non-Plated Hole Size

Plated Hole Size

Board Slots

Non-Plated Slot Size

Plated Slot Size

Board Square Holes

Non-Plated Square Hole Size

Plated Square Hole Size

Other

Top Layer Annular Ring Size

Mid Layer Annular Ring Size

Bottom Layer Annular Ring Size

Pad Solder Mask

Pad Paste Mask

Pad Pwr/Gnd Expansion

Pad Relief Conductor Width

Pad Relief Air Gap

Pad Relief Entries

Via Solder Mask

Via Pwr/Gnd Expansion

Track Width

Arc Line Width

Arc Radius

Arc Degrees

Text Height

Text Width

Net Track Width

Net Via Size

## Board Specification

General
Board Size | 3543.307mils x 3385.827mils
Components on board | 48

Back to top

## Routing

Routing Information
Routing completion | 100.00%
Connections | 188
Connections routed | 188
Connections remaining | 0

Back to top

## Layer Information

Layer | Arcs | Pads | Vias | Tracks | Texts | Fills | Regions | ComponentBodies
Top Layer | 0 | 111 | 0 | 288 | 0 | 4 | 146 | 0
Bottom Layer | 0 | 0 | 0 | 175 | 0 | 2 | 153 | 0
Mechanical 1 | 2 | 0 | 0 | 0 | 0 | 0 | 0 | 2
Mechanical 13 | 0 | 0 | 0 | 54 | 0 | 0 | 0 | 34
Mechanical 15 | 0 | 0 | 0 | 42 | 0 | 0 | 0 | 0
Top Overlay | 37 | 0 | 0 | 3857 | 154 | 2 | 0 | 0
Bottom Overlay | 0 | 0 | 0 | 0 | 0 | 0 | 0 | 0
Top Paste | 0 | 0 | 0 | 0 | 0 | 0 | 0 | 0
Bottom Paste | 0 | 0 | 0 | 0 | 0 | 0 | 0 | 0
Top Solder | 0 | 0 | 0 | 0 | 0 | 0 | 0 | 0
Bottom Solder | 0 | 0 | 0 | 0 | 0 | 0 | 0 | 0
Drill Guide | 0 | 0 | 0 | 0 | 0 | 0 | 0 | 0
Keep-Out Layer | 6 | 0 | 0 | 4 | 0 | 0 | 2 | 0
Drill Drawing | 0 | 0 | 0 | 0 | 0 | 0 | 0 | 0
Multi-Layer | 0 | 132 | 37 | 0 | 0 | 0 | 3 | 0
Total | 45 | 243 | 37 | 4420 | 154 | 8 | 304 | 36

Back to top

Drill Pairs | Vias
Top Layer - Bottom Layer | 37
Total | 37

Back to top

## Board Holes

Non-Plated Hole Size | Pads | Vias
Total | 0 | 0

Back to top

Plated Hole Size | Pads | Vias
0mils | 111 | 0
12mils | 0 | 33
35.433mils | 125 | 0
45mils | 2 | 0
125.984mils | 0 | 4
Total | 238 | 37

Back to top

## Board Slots

Non-Plated Slot Size / Length | Pads
Total | 0

Back to top

Plated Slot Size / Length | Pads
19.685mil / 78.74mil | 2
47.244mil / 70.866mil | 3
Total | 5

Back to top

## Board Square Holes

Non-Plated Square Hole Size | Pads
Total | 0

Back to top

Plated Square Hole Size | Pads
Total | 0

Back to top

## Other

Top Layer Annular Ring Size | Count
13mils | 32
23mils | 1
23.622mils | 125
31.496mils | 4
45mils | 2
98.425mils | 2
110.236mils | 3
Total | 169

Back to top

Mid Layer Annular Ring Size | Count
13mils | 32
23mils | 1
23.622mils | 125
31.496mils | 4
45mils | 2
98.425mils | 2
110.236mils | 3
Total | 169

Back to top

Bottom Layer Annular Ring Size | Count
13mils | 32
23mils | 1
23.622mils | 125
31.496mils | 4
45mils | 2
98.425mils | 2
110.236mils | 3
Total | 169

Back to top

Pad Solder Mask | Count
4mils | 243
Total | 243

Back to top

Pad Paste Mask | Count
0mils | 243
Total | 243

Back to top

Pad Pwr/Gnd Expansion | Count
20mils | 243
Total | 243

Back to top

Pad Relief Conductor Width | Count
10mils | 243
Total | 243

Back to top

Pad Relief Air Gap | Count
10mils | 243
Total | 243

Back to top

Pad Relief Entries | Count
4 | 243
Total | 243

Back to top

Via Solder Mask | Count
4mils | 37
Total | 37

Back to top

Via Pwr/Gnd Expansion | Count
20mils | 37
Total | 37

Back to top

Track Width | Count
0.8mils | 1137
1.2mils | 2418
1.969mils | 16
3.937mils | 75
7.874mils | 207
8mils | 12
9.843mils | 4
10mils | 84
15mils | 201
15.748mils | 4
18mils | 29
20mils | 2
25mils | 61
30mils | 20
35mils | 20
40mils | 9
50mils | 41
52mils | 12
55mils | 41
65mils | 27
Total | 4420

Back to top

Arc Line Width | Count
7.874mils | 35
10mils | 3
11.811mils | 2
15.748mils | 5
Total | 45

Back to top

Arc Radius | Count
5.906mils | 2
7.874mils | 1
15.748mils | 16
15.748mils | 16
19.685mils | 2
22mils | 2
60mils | 1
94.092mils | 1
157.48mils | 4
Total | 45

Back to top

Arc Degrees | Count
45 | 1
90 | 36
360 | 8
Total | 45

Back to top

Text Height | Count
60mils | 149
90mils | 1
100mils | 1
137.795mils | 1
160mils | 2
Total | 154

Back to top

Text Width | Count
10mils | 154
Total | 154

Back to top

Net Track Width | Count
10mils | 49
Total | 49

Back to top

Net Via Size | Count
39.37mils | 49
Total | 49

Back to top

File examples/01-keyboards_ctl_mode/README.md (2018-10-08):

# PyESPCar按键控制模式

mqtt control

使用PyGame做键盘事件监听，然后映射到`pyespcar sdk`的方法上面。

运行程序：

```bash
sudo python3 keyboards_ctl_mode.py
```

注意要选中当前的PyGame的窗口

**键盘与功能映射**

| 按键 | PyGame中的按键标识 | 功能描述 |
| --- | --- | --- |
| 空格键 | K_SPACE | 小车停止 |
| 字母键-W  | K_w | 云台向上旋转 |
| 字母键-A  | K_a | 云台向左旋转 |
| 字母键-S  | K_s | 云台向下旋转 |
| 字母键-D  | K_d | 云台向右旋转 |
| 方向键-左 | K_LEFT | 小车向左转 |
| 方向键-右 | K_RIGHT | 小车向右转 |
| 方向键-上 | K_UP | 小车前进 |
| 方向键-下 | K_DOWN | 小车后退 |

同时你也可以将手机挂载到小车上，打开IP摄像头APP，感受实时图传的体验， 效果视频见：

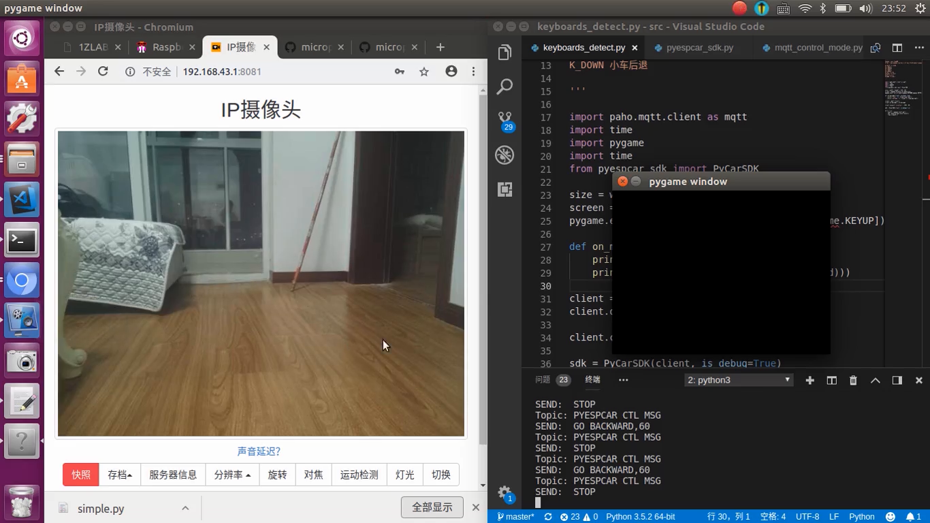
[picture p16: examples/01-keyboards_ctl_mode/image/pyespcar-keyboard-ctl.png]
远程控制


`./video/PyESPCar键盘控制+手机WIFI图传.mkv`

APP的使用教程见：

[IP摄像头APP与OpenCV视频流读取-1Z实验室](https://www.jianshu.com/p/0586d7dad113)

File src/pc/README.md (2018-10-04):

# 测试PyESPCar-SDK

在当前目录下运行`ipython/Jupyter`

把下面的内容粘贴进去

`test_pyespcar.py`

```python
import paho.mqtt.client as mqtt
from pyespcar_sdk import PyCarSDK

mqtt_client = mqtt.Client()
# mqtt_client.on_message = on_message
mqtt_client.connect('localhost', 1883, 60)
sdk = PyCarSDK(mqtt_client, is_debug=True)
```

然后你就可以测试`sdk`对象的各种方法了。

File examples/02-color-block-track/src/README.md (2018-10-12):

# PyESPCar色块追踪使用说明

## 工程文件说明

| 文件 | 备注 |
| --- | --- |
| car_config.py | 小车的配置文件 |
| pyespcar_sdk.py | PyESPCar的SDK |
| pid.py | PID控制的库 |
| wifi_camera.py | IP摄像头的类 |
| car_state.py | 定义了小车的各种状态 |
| object_tracker.py | 物体追踪类 |
| cvutils.py | 自定义了一些CV小工具 |
| color_block_finder_node.py | 色块识别的节点, 发送识别出的色块信息给物体追踪节点 |
| object_tracker_node.py | 物体追踪节点, 发送控制指令给PyESPCar |

## 开发配置

### IP摄像头

这里我们使用了一个名字叫做IP摄像头APP,把手机作为了WIFI摄像头. 使用教程见:

[IP摄像头APP与OpenCV视频流读取-1Z实验室](https://www.jianshu.com/p/0586d7dad113)

### 配置色块识别节点

这里你需要修改一下这个Phone的IP, 从上面的APP画面中获得.

```python
# 创建一个IP摄像头对象
phone_ip = '192.168.43.1'
```

## 操作流程

### 1.打开PyESPCar

打开PyESPCar， 默认上电执行MQTT模式的代码，把色块放在手机摄像头的可视区域内。

同时开启IPCamera的APP。

### 2.色块识别节点 ColorBlockFinder

识别色块，并且将色块举例画面的偏移量，以及面积的偏移量，通过MQTT发送给**物体追踪节点**。

```bash
python3 color_block_finder_node.py
```

刚开始执行程序的时候, 需要截取当前画面中的色块部分（**SelectROI**）, 选中后回车表示确认。

接下来，使用**直方图反向投影** 进行色块识别，不需要手动调节阈值

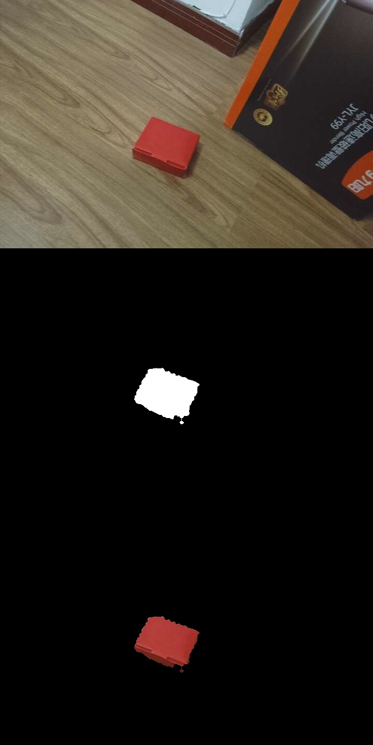
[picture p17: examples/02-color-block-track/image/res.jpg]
res


### 3.物体追踪节点 ObjectTracker

在另外一个终端， 运行下面的指令：

```bash
python3 object_tracker_node.py
```

该节点，会接收来自**色块识别节点ColorBlockFinder** 的偏移量信息，进而计算得到PyESPCar的控制指令，并通过MQTT发送给PyESPCar。

在这个代码里面，我们用到了 **有限状态机 Finite State Machine。 **， 并通过Python的状态(State)设计模式实现该算法。

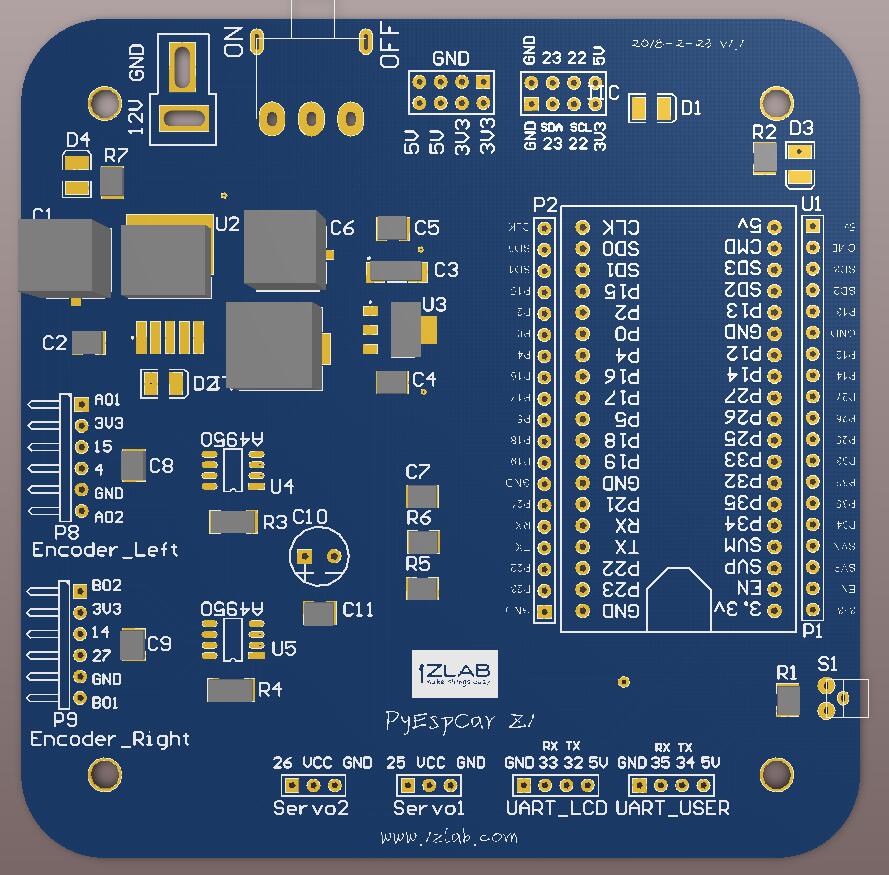
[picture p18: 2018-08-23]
image/boards.jpg

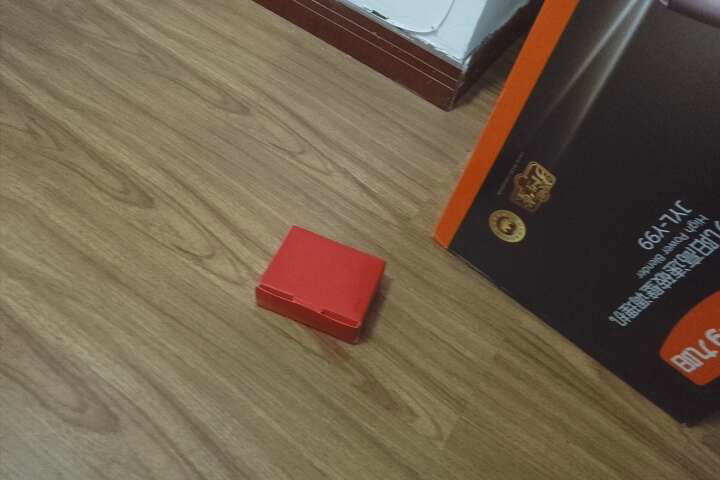
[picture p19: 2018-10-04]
examples/02-color-block-track/image/screenshot.png

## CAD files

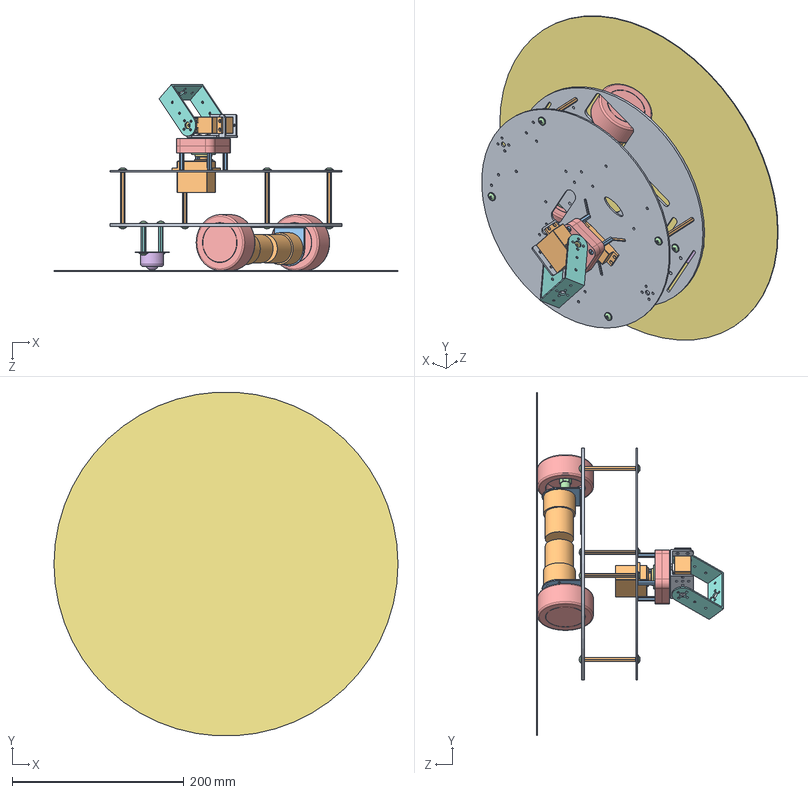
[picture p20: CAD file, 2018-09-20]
hardware/设计文件/v2.0/小车整体.SLDASM
400.0 x 399.3 x 217.2 mm
底盘
电机 x 2
电机支架 x 2
联轴器 x 2
轮胎 x 2
牛眼万向轮
座子
铜柱M4x30 双通 x 2
中间板
铜柱M4x60 双通 x 4
铜柱M3x18双通 x 4
轴 x 2
轴承座 x 2
deep groove ball bearings gb
舵盘 x 2
长U
多功能支架
DS3119MG x 2
countersunk slotted raised head screw_din x 8
DIN 967 - M4 x 6 - Z --- 4.6S x 12

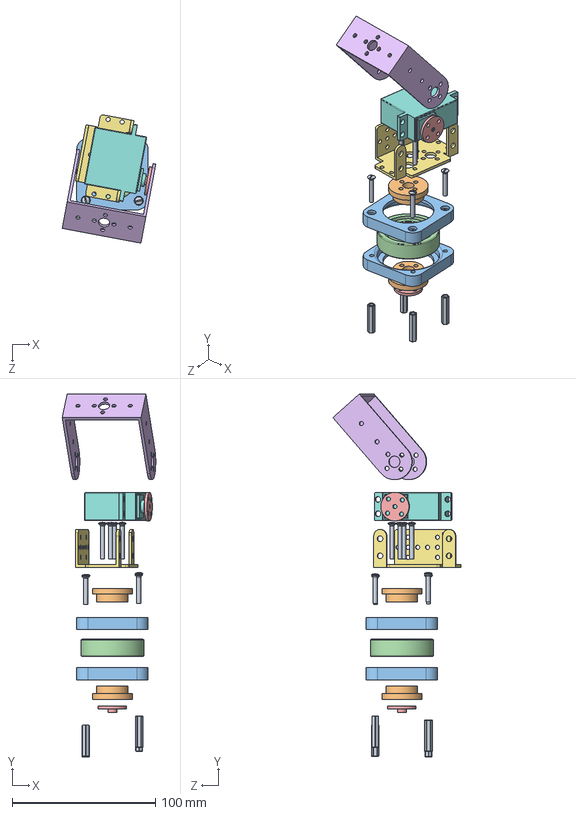
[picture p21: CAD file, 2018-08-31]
hardware/设计文件/v2.0/云台部分-v2.0/云台.SLDASM
65.4 x 253.6 x 89.6 mm
铜柱M3x18双通 x 4
轴 x 2
轴承座 x 2
deep groove ball bearings gb
舵盘 x 2
长U
多功能支架
DS3119MG
countersunk slotted raised head screw_din x 8

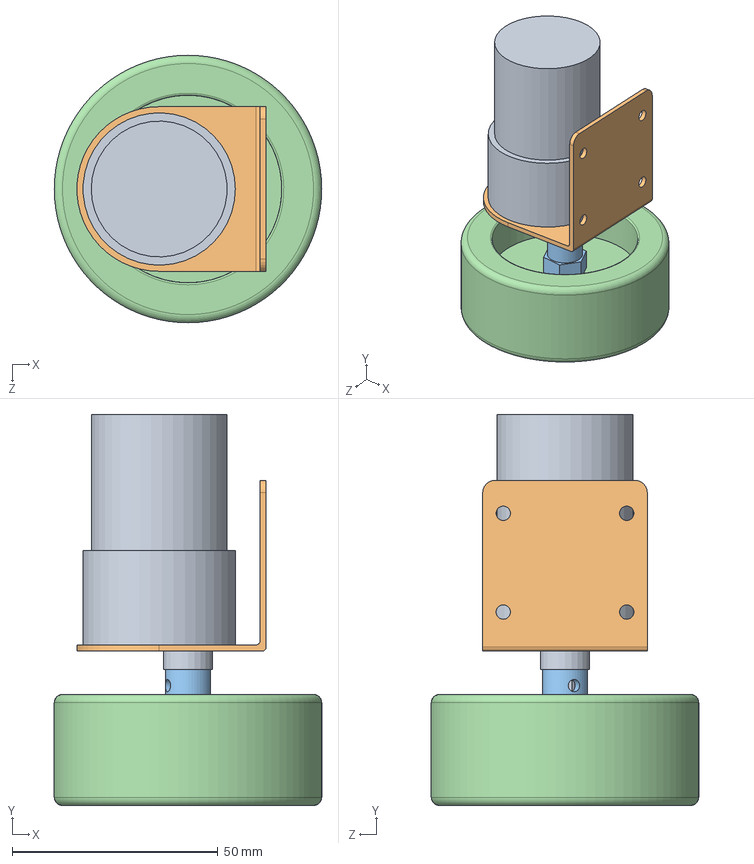
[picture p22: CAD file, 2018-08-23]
hardware/设计文件/v2.0/动力部分/电机部分.SLDASM
65.0 x 95.0 x 65.0 mm
电机
电机支架
联轴器
轮胎

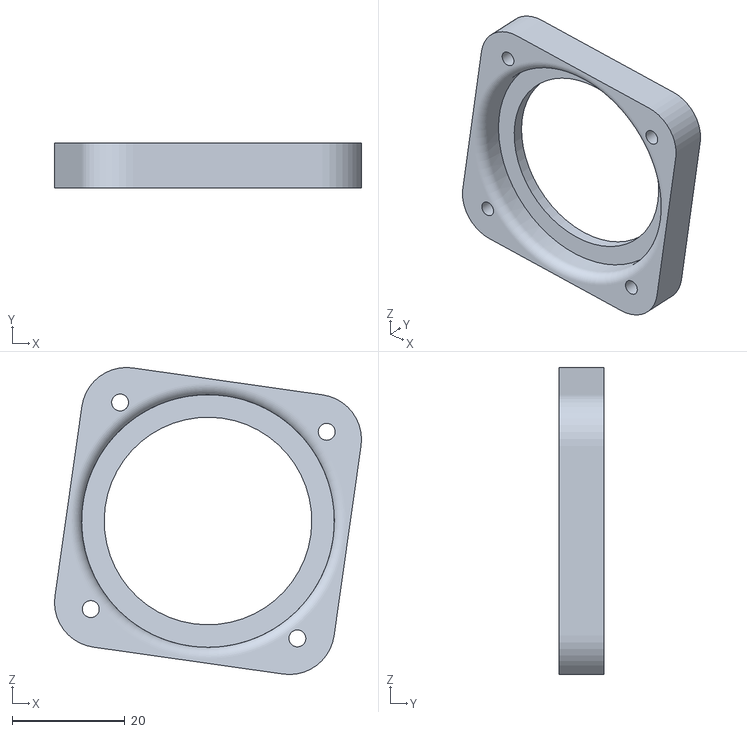
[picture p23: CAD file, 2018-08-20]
hardware/加工图纸模型/云台打印文件/云台 - 轴承座-2.STL
54.4 x 8.00 x 54.4

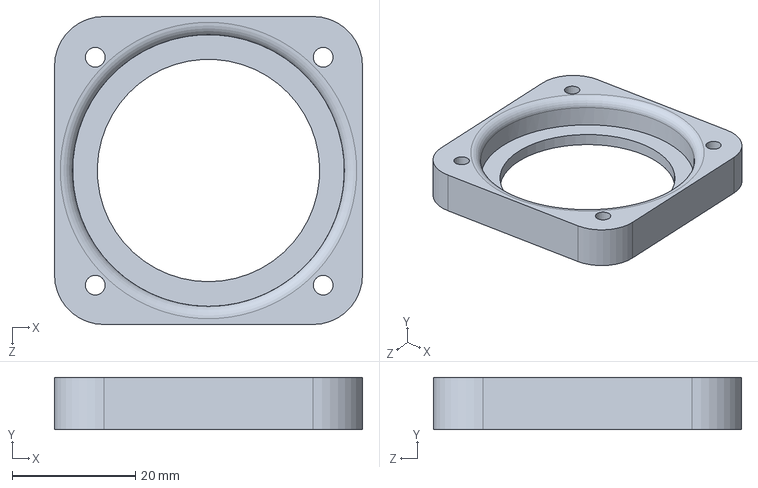
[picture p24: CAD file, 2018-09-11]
hardware/设计文件/v2.0/云台部分-v2.0/轴承座.SLDPRT
50.0 x 8.50 x 50.0 mm

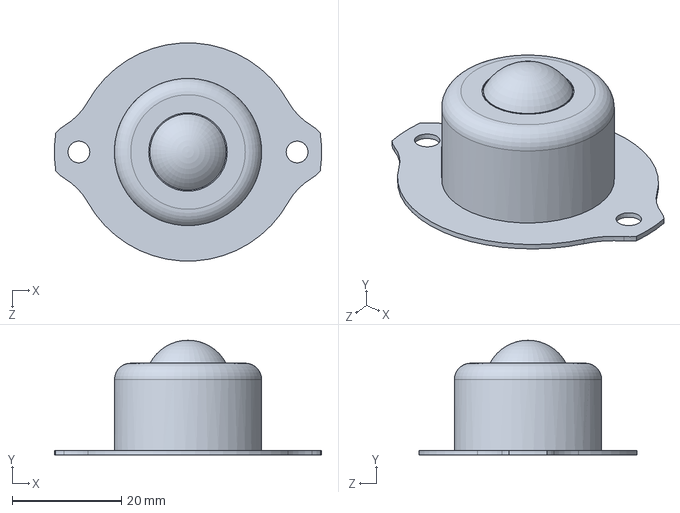
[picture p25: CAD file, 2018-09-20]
hardware/设计文件/v2.0/动力部分/牛眼万向轮.SLDPRT
48.9 x 21.0 x 39.9 mm

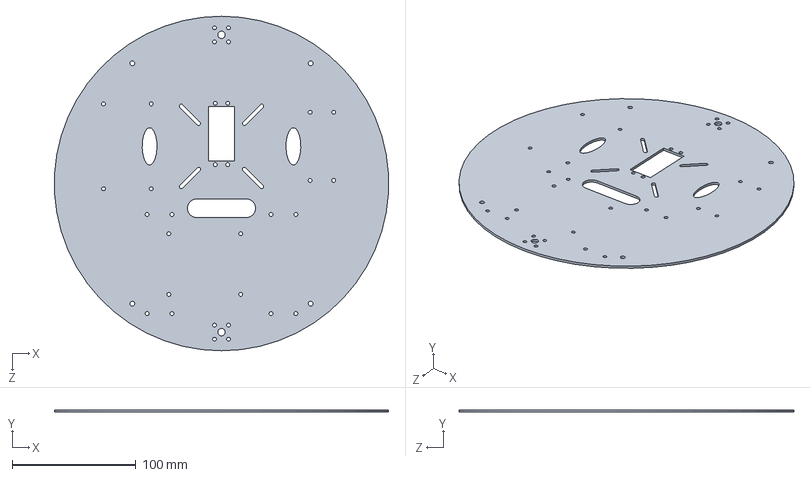
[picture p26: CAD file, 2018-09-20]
hardware/设计文件/v2.0/车身部分/中间板.SLDPRT
269.5 x 2.00 x 270.0 mm

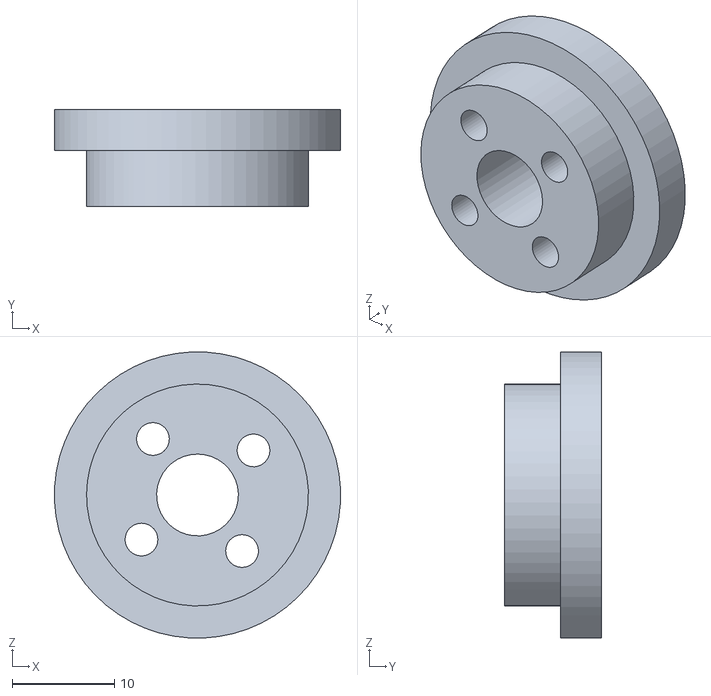
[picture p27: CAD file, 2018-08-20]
hardware/加工图纸模型/云台打印文件/云台 - 轴-2.STL
28.0 x 9.50 x 28.0

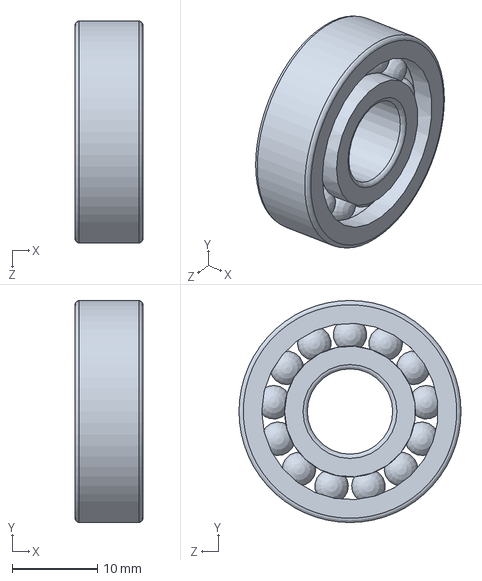
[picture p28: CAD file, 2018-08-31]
hardware/设计文件/v2.0/云台部分-v2.0/deep groove ball bearings gb.sldprt
8.00 x 26.0 x 26.0 mm

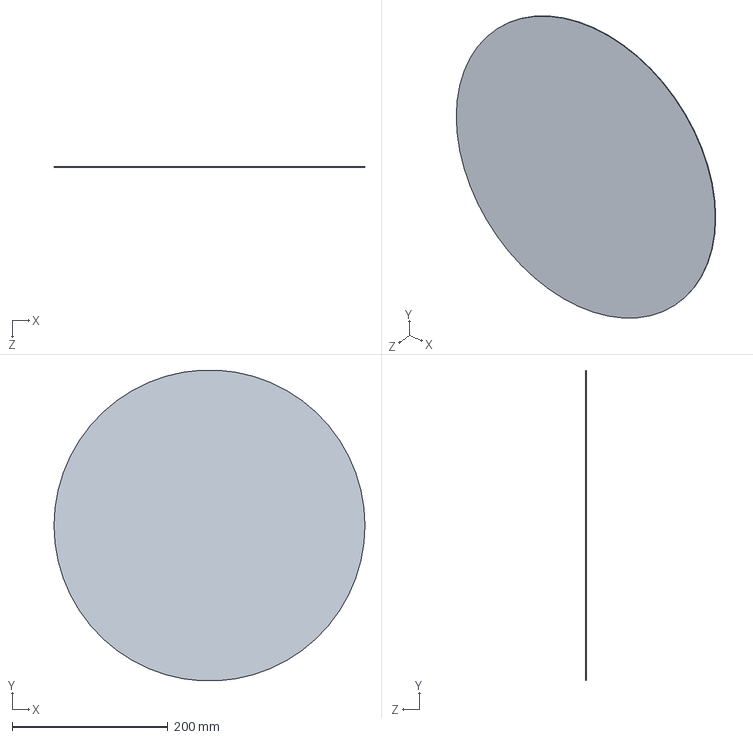
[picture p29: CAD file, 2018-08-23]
hardware/设计文件/v2.0/座子.SLDPRT
400.0 x 399.3 x 1.00 mm

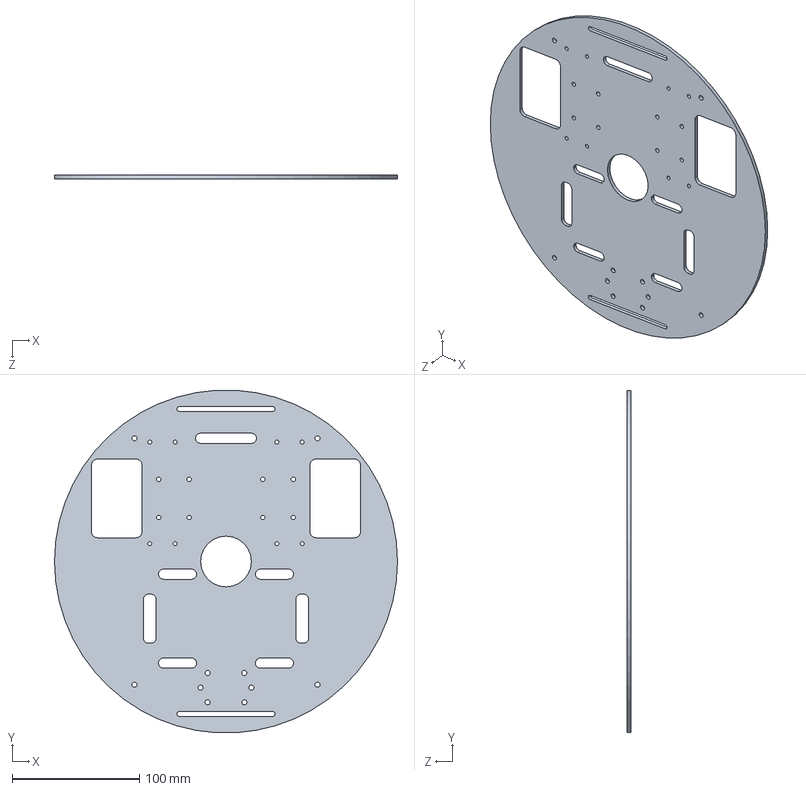
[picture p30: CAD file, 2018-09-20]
hardware/设计文件/v2.0/车身部分/底盘.SLDPRT
270.0 x 269.5 x 3.00 mm

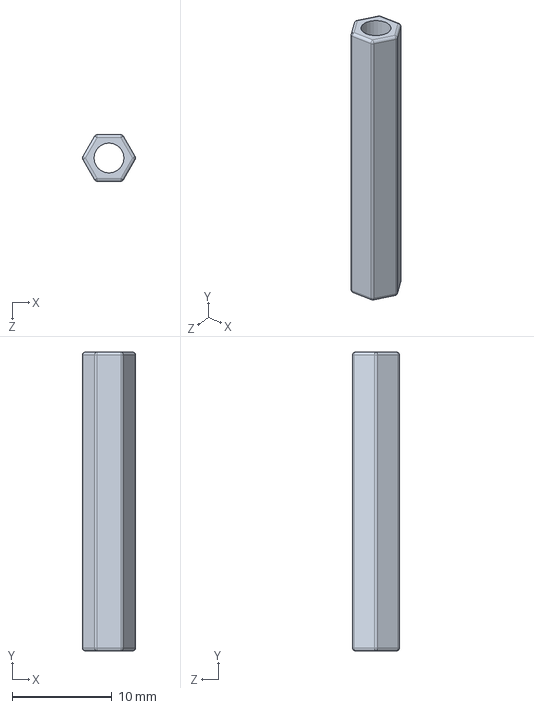
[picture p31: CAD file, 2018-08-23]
hardware/设计文件/v2.0/车身部分/铜柱M4x30 双通.SLDPRT
5.33 x 30.0 x 4.70 mm

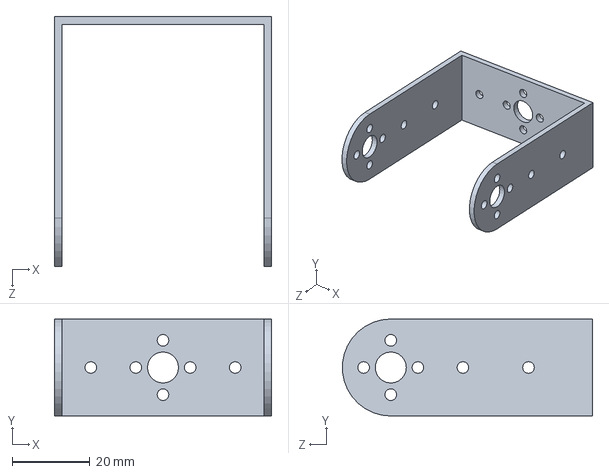
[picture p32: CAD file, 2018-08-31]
hardware/设计文件/v2.0/云台部分-v2.0/长U.SLDPRT
56.0 x 25.0 x 64.4 mm

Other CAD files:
hardware/PCB文件/v2.2/PCB尺寸.DWG
hardware/加工图纸模型/底盘金属加工图纸/中间板(2mm).DWG
hardware/加工图纸模型/底盘金属加工图纸/标注图纸/底盘（2mm）.DWG
hardware/加工图纸模型/底盘金属加工图纸/底盘(2mm).DWG
hardware/加工图纸模型/底盘金属加工图纸/标注图纸/中间板（2mm）.DWG
hardware/设计文件/v1.1/云台部分 - v1.1/DS3119MG.SLDPRT
hardware/设计文件/v1.1/云台部分 - v1.1/云台.SLDASM
hardware/设计文件/v1.1/云台部分 - v1.1/多功能支架.SLDPRT
hardware/设计文件/v1.1/云台部分 - v1.1/舵机座.SLDPRT
hardware/设计文件/v1.1/云台部分 - v1.1/舵盘.SLDPRT
hardware/设计文件/v1.1/云台部分 - v1.1/轴.SLDPRT
hardware/设计文件/v1.1/云台部分 - v1.1/轴承60-22 GB 276-94.sldprt
hardware/设计文件/v1.1/云台部分 - v1.1/轴承座.SLDPRT
hardware/设计文件/v1.1/云台部分 - v1.1/铜柱M3x22双通.SLDPRT
hardware/设计文件/v1.1/动力部分/牛眼万向轮.SLDPRT
hardware/设计文件/v1.1/动力部分/电机.SLDPRT
hardware/设计文件/v1.1/动力部分/电机支架.SLDPRT
hardware/设计文件/v1.1/动力部分/碟形万向轮.SLDPRT
hardware/设计文件/v1.1/动力部分/联轴器.SLDPRT
hardware/设计文件/v1.1/动力部分/轮胎.SLDPRT
hardware/设计文件/v1.1/小车整体.SLDASM
hardware/设计文件/v1.1/车身部分/中间板.SLDPRT
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

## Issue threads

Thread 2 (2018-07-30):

电池电压ADC采样，使用平滑滤波

mushroom-x, 2018-07-30:

mushroom-x, 2018-08-22:
实际上是 7v  测得的是5.8v  差距过大

mushroom-x, 2018-08-22:
问题解决了，公式没错，可能跟当前测试用的ESP32开发板有关系。
ESP32开发板的35号引脚接了扬声器，所以会干扰结果。

Closed 2018-08-22.

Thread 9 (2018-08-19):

小车波形数据可视化

mushroom-x, 2018-08-19:
用于PID参数调节。

mushroom-x, 2018-08-20:
借助串口示波器软件SerialTool  https://github.com/gztss/SerialTool

mushroom-x, 2018-08-20:
小峰写的测试程序
小峰写的测试程序

```python

import struct

class SendWave:
    def __init__(self,Channel_cnt=16,Value_type='Int16'):
        '''
        Oscilloscope 初始化
        SendWave(UART,Channel_cnt=16,Value_type='Int16')
        Channel_cnt         ---开启通道个数，在同步传输的时候会用到
        Value_type          -- 数据类型，Int8，Int16，Int32，Float
        '''
        self.Ch_Num          = Channel_cnt
        self.Frame_Head      = 163      #帧头识别字
        self.Frame_PointMode = 168      #点模式识别字
        self.Frame_SyncMode  = 169      #同步模式识别字
        self.Frame_InfoMode  = 170      #信息帧识别字
        self.buffer =  []               #数据缓存区
        self.Format_type = Value_type   #数据格式信息

        self.types = {'Int8':(16,'BBBb','Bb'),
                      'Int16':(32,'BBBh','Bh'),
                      'Int32':(48,'BBBi','Bi'),
                      'Float':(0,'BBBf','Bf')}
        self.Format=self.types[self.Format_type][1]

    def ws_point(self,*values):
        data = ''
        patten = ''
        Channels = len(values)
        if Channels > 0 and Channels<17:
            for Channel in range(Channels):
                self.buffer.append(self.Frame_Head)
                self.buffer.append(self.Frame_PointMode)
                self.buffer.append(Channel | self.types[self.Format_type][0]) # 通道及数据格式信息
                self.buffer.append(values[Channel]); # 数据        
            patten = '>'+self.Format*Channels
            data = struct.pack(patten,*self.buffer)
            self.buffer = []
        return data

    def ws_sync(self,*values):
        data = ''
        patten = ''
        Channels = len(values)

        self.buffer.append(self.Frame_Head)
        self.buffer.append(self.Frame_SyncMode)

        if Channels > 0 and Channels<17:
            for Channel in range(Channels):
                self.buffer.append(Channel | self.types[self.Format_type][0]) # 通道及数据格式信息    
                self.buffer.append(values[Channel]); # 数据
            patten = '>'+self.Format+self.types[self.Format_type][2]*(Channels-1)
            data = struct.pack(patten,*self.buffer)
            self.buffer = []
        return data
        
'''
import sendwave
import random
import time

osc = sendwave.SendWave()
value = [random.randint(20, 2000) for x in range(16)]

data = osc.ws_sync(*value)
print(data)
data = osc.ws_point(*value)
print(data)

'''
```

mushroom-x, 2018-08-22:
想用 Tkinter 写个上位机， 这样可以更加灵活方便

Closed 2018-08-25.

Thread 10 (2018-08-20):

制作编码器计数模块

mushroom-x, 2018-08-20:
MicroPython-ESP32 性能不能用来稳定读取编码器的值

mushroom-x, 2018-08-20:
这个是整个项目停滞不前的关键因素

mushroom-x, 2018-08-22:
小峰提供的Encoder库已经解决了这个问题

Closed 2018-08-22.

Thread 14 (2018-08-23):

修改管脚并重新测试

mushroom-x, 2018-08-23:
新版本的映射
-----------------------------------------------------
```python
'''
小车的管脚配置
'''
# GPIO字典
gpio_dict = {
    "BATTERY_ADC": 36, # 电池ADC采样(SVN)
    "USER_BUTTON": 39, # 用户按键(SVP)

    "LEFT_MOTOR_A": 17, # 左侧电机A相
    "LEFT_MOTOR_B": 5, # 左侧电机B相

    "RIGHT_MOTOR_A": 18, # 右侧电机A相
    "RIGHT_MOTOR_B": 19, # 右侧电机B相

    "LEFT_ENCODER_A": 15, # 左侧编码器A相
    "LEFT_ENCODER_B": 4, # 左侧编码器B相

    "RIGHT_ENCODER_A": 14, # 右侧编码器A相
    "RIGHT_ENCODER_B": 27, # 右侧编码器B相

    "UART_LCD_RX": 33, # 串口液晶屏 接收端
    "UART_LCD_TX": 32 # 串口液晶屏 发送端

    "UART_USER_RX": 35, # 用户串口接收端
    "UART_USER_TX": 34 # 用户串口 发送端

    "USER_IIC_SCL": 22, # 用户IIC SCL
    "USER_IIC_SDA": 23 # 用户IIC SDA

    "SERVO_1": 25, # 舵机1
    "SERVO_2": 26 # 舵机2

}
```

Closed 2018-08-25.

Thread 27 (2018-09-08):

电机角度控制的时候, 徒手旋转电机, 正向旋转一丢丢, 编码器自增非常大的值, 反向就没有问题

mushroom-x, 2018-09-08:
头大啊 ,为什么会这样

mushroom-x, 2018-09-08:
也有时候,硬掰过去之后,停止, 编码器度数就开始自增.

mushroom-x, 2018-09-08:
在小车实际测试的时候,因为存在这个问题, 导致car测试的时候, 每次前进一段时间,刹车,因为惯性, 小车会往前走一点点, 这个时候,因为存在上述的问题, 编码器度数突增, 小车就开始缓慢向后退.

mushroom-x, 2018-09-08:
'LEFT_MOTOR_INSTALL_DIR': False, # 左侧电机的安装方向
    'LEFT_ENCODER_IS_REVERSE': False, # 左侧编码器是否为反

改为

'LEFT_MOTOR_INSTALL_DIR': True, # 左侧电机的安装方向
    'LEFT_ENCODER_IS_REVERSE': True, # 左侧编码器是否为反

编码器值突变的问题还没有出现, 向后旋转,依然有较大阻力,

说明跟算法有关

mushroom-x, 2018-09-09:
重构了Motor 正反转不一样的问题 不存在了, 问题就出现电机启动的时候, 或从 停止到扰动的时候.
噪声比较大,导致无法读出编码器的读数.

解决这个问题的方法
1. 如果25ms内采样的数值超过正常值就舍弃
2. 位置使用 速度的积分, 每次测速都清零.

mushroom-x, 2018-09-13:
改用积分, 问题已解决

Closed 2018-09-13.

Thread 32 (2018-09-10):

测试舵机控制的时候电机也会转

mushroom-x, 2018-09-10:
底部舵机 PWM = 0 ,或者100 的时候 电机就会旋转?

```python
from machine import Pin,PWM

pwm_freq = 50

servo_bottom = PWM(Pin(27, Pin.OUT), freq=pwm_freq)
servo_top = PWM(Pin(12, Pin.OUT), freq=pwm_freq)

servo_bottom.duty(77)
servo_top.duty(80)
```

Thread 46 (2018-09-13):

PCB 生产过程中部分管脚标识缺失.

mushroom-x, 2018-09-13:
? 生产的时候, 乱码问题

rose-w, 2018-09-13:
已经和店家核对，修改乱码问题

Closed 2018-09-13.

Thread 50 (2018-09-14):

速度控制改用增量式PID

mushroom-x, 2018-09-14:
之前智障了  用了位置PID控制的电机转速.

```
Pwm +=Kp[e(k)-e(k-1)]+Ki*e(k)+Kd[e(k)-2e(k-1)+e(k-2)]
```

电机角度控制, 可以用离散PID控制
```
Pwm =Kp*e(k)+Ki*∑e(k)+Kd[e(k)-e(k-1)]
```

mushroom-x, 2018-09-14:
同时也改写电机角度控制代码.

mushroom-x, 2018-09-17:
完成增量式PID速度控制

Closed 2018-09-17.

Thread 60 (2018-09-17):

ESP32相映外部中断IRQ性能的问题

mushroom-x, 2018-09-17:
在PWM > 300 左右的时候，编码器计数就开始失灵了
此时转速 -> 35度 / 35ms

（35/360 × 1320） / （1000 / 35） = 3666

1s内相应的中断是3666

ESP32的中断相应分辨率为： 0.2727769 ms

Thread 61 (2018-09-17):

ESP32相映外部中断IRQ性能的问题

mushroom-x, 2018-09-17:
在PWM > 300 左右的时候，编码器计数就开始失灵了
此时转速 -> 35度 / 35ms

（35/360 × 1320） / （1000 / 35） = 3666

1s内相应的中断是3666

ESP32的中断相应分辨率为： 0.2727769 ms

mushroom-x, 2018-09-17:
取消四倍频， 可正常使用测速

Closed 2018-09-17.

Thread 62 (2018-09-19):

PyESCar插上乐鑫的DevKit之后经有时候会进入下载模式

mushroom-x, 2018-09-19:
是不是跟P2有关系？
报错信息如下：

```
➜  src git:(master) ✗ esp32-link
picocom v1.7

port is        : /dev/ttyUSB0
flowcontrol    : none
baudrate is    : 115200
parity is      : none
databits are   : 8
escape is      : C-a
local echo is  : no
noinit is      : no
noreset is     : no
nolock is      : no
send_cmd is    : sz -vv
receive_cmd is : rz -vv
imap is        :
omap is        :
emap is        : crcrlf,delbs,

Terminal ready
ets Jun  8 2016 00:22:57

rst:0x1 (POWERON_RESET),boot:0x3 (DOWNLOAD_BOOT(UART0/UART1/SDIO_REI_REO_V2))
waiting for download
ets Jun  8 2016 00:22:57

rst:0x1 (POWERON_RESET),boot:0x3 (DOWNLOAD_BOOT(UART0/UART1/SDIO_REI_REO_V2))
waiting for download
ets Jun  8 2016 00:22:57

rst:0x1 (POWERON_RESET),boot:0x3 (DOWNLOAD_BOOT(UART0/UART1/SDIO_REI_REO_V2))
waiting for download
ets Jun  8 2016 00:22:57
```

mushroom-x, 2018-09-20:
rst:0x1 (POWERON_RESET),boot:0x3 (DOWNLOAD_BOOT(UART0/UART1/SDIO_REI_REO_V2))
waiting for download

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

mushroom-x, 2018-09-20:
如何为 ESP 系列模组烧录固件
http://wiki.ai-thinker.com/esp_download

mushroom-x, 2018-09-20:
把ESP32的P0管脚拔下来（杜邦线），问题就解决了
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

Closed 2018-09-29.

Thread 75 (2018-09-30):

有时候PC上的MQTTClient会跟MQTT Broker断开连接

mushroom-x, 2018-09-30:
需要执行这一句才能正常连接
```python
sdk.mqtt_client.connect('localhost')
```

mushroom-x, 2018-09-30:
是发送高频的MQTT请求会被 断开连接么？

mushroom-x, 2018-09-30:
还是超过特定的时间就自动断开了？

mushroom-x, 2018-09-30:
MicroPython-ESP32 MQTT通信有时候也会出现连不上的情况

mushroom-x, 2018-09-30:
尝试Labo的固件

mushroom-x, 2018-10-02:
其实是我在代码中的类型转换出了问题 `int('1.0')` 会报错， 改成`int(float('1.0'))` 就可以了

Closed 2018-10-02.

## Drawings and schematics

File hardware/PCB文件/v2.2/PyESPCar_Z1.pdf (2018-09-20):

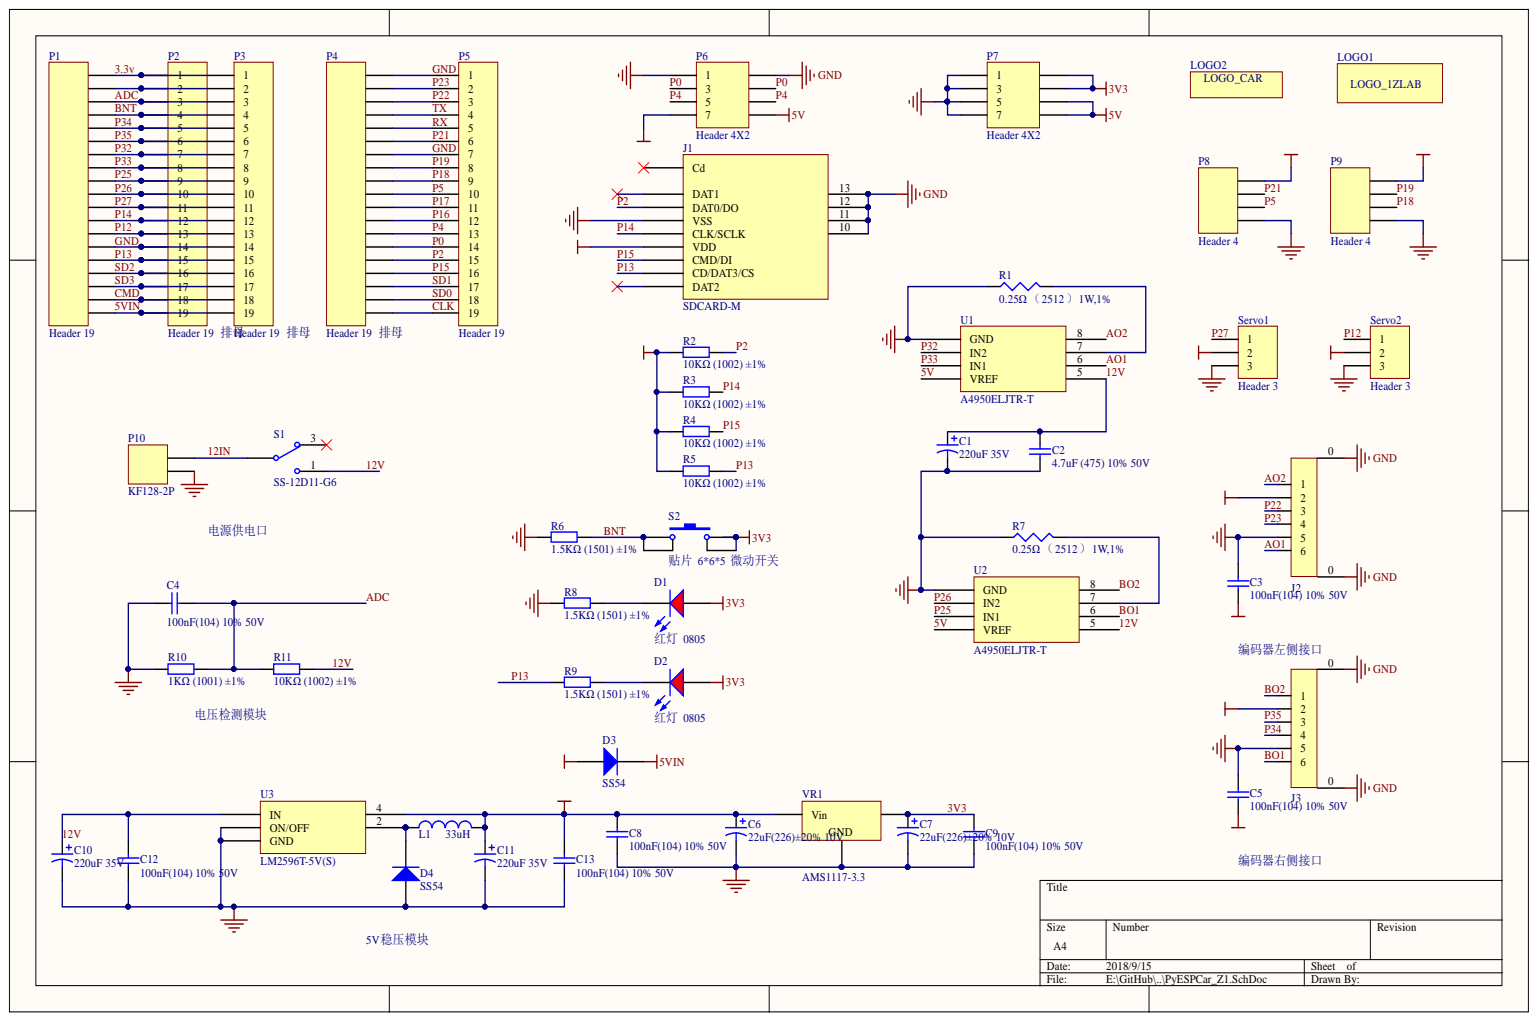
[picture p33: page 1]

12V | | L1 33uH
LM2596T-5V(S) C10

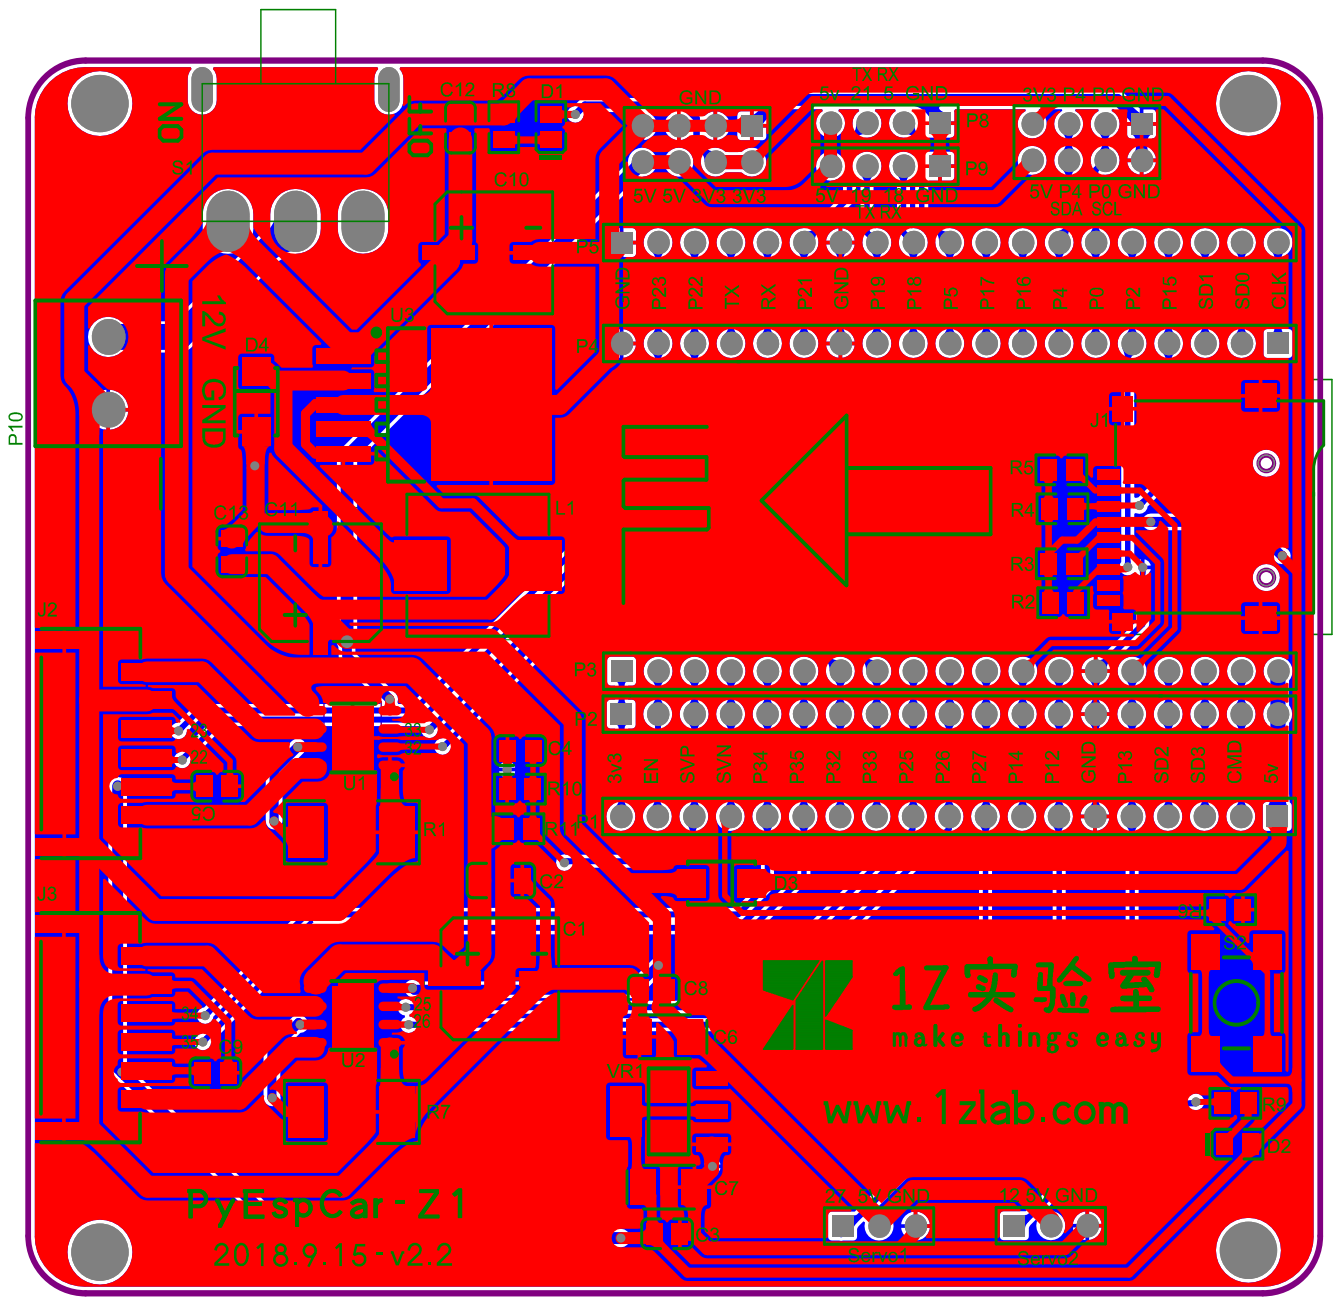
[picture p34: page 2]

Comment | Description | Designator | Footprint | LibRef | Quantity
0.25Ω （2512 ） 1W,1% | 超低阻值电阻 | R1, R7 | 2512 | Res3 | 2
1KΩ (1001) ±1% | 贴片电阻 | R10 | 0805_R | 0805 1KΩ (1001) 1% | 1
1.5KΩ (1501) ±1% | 贴片电阻 | R6, R8, R9 | 0805_R | 0603 1.5KΩ (1501) 1% | 3
4.7uF (475) 10% 50V | 贴片电容 | C2 | 1206_C | 1206 4.7uF (475) 10% 50V | 1
10KΩ (1002) ±1% | 贴片电阻 | R2, R3, R4, R5, R11 | 0805_R | 0805 1KΩ (1001) 1% | 5
22uF(226)±20% 10V | 钽电容 | C6, C7 | CAP-3528 | Cap Pol | 2
33uH ±20% | 功率电感 MS104R-330MT | L1 | CAPM100100X103 N | Inductor | 1
100nF(104) 10% 50V | 贴片电容 | C3, C4, C5, C8, C9, C12, C13 | 0805_C | 0805 100nF(104) 10% 50V | 7
220uF 35V | 贴片电解电容 , 贴片 铝解电容 , 贴片铝解 电容 | C1, C10, C11 | CAPM8485X103N | Cap Pol1 | 3
A4950ELJTR-T | A4950 电机驱动 , A4950 电机驱动 | U1, U2 | SOP-8_EP_150mil | A4950 | 2
AMS1117-3.3 | 低压差线性稳压 (LDO) | VR1 | SOT-223 | SOT-223 AMS1117-3.3 | 1
Header 3 | Header, 3-Pin | Servo1, Servo2 | HDR1X3 | Header 3 | 2
Header 4 | Header, 4-Pin | P8, P9 | HDR1X4 | Header 4 | 2
Header 4X2 | Header, 4-Pin, Dual row | P6, P7 | HDR2X4 | Header 4X2 | 2
Header 19 | Header, 19-Pin 排 针 | P1, P5 | HDR1X19 | Header 19 | 2
Header 19 排母 | Header, 19-Pin 排 母 | P2, P3, P4 | HDR1X19 | Header 19 | 3
KF128-2P | 5.08mm 端子 | P10 | HDR2X1_D1 | Header 2 | 1
LM2596T-5V(S) | 稳压芯片 | U3 | TO-263-5 | LM2596T-5V(S) | 1
LOGO_1ZLAB | | LOGO1 | 1ZLAB_LOGO | LOGO_1ZLAB | 1
LOGO_CAR | | LOGO2 | car_logo | LOGO_CAR | 1
PH-PS-2.0-6 | PH-PS-2.0-6 | J2, J3 | PH-PS-2.0-6 | PH-PS-2.0-6 | 2
SDCARD-M | TF卡槽 | J1 | SDCARD-M | SDCARD-M | 1
SS54 | 二极管 | D3, D4 | SMA(DO-214AC)_S1 | SMA(DO-214AC) SS54 | 2
SS-12D11-G6 | 拨动开关 2档带固定 脚黑色短柄 3脚侧 | S1 | SW-3 | SW-SPDT | 1
红灯 0805 | 发光二极管 | D1, D2 | 0805_LED_S1 | 0805 红灯 | 2
贴片 6*6*5 微动开关 | 贴片 6*6*5 微动开关 | S2 | SW_PB4_A1 | SW-PB4 | 1

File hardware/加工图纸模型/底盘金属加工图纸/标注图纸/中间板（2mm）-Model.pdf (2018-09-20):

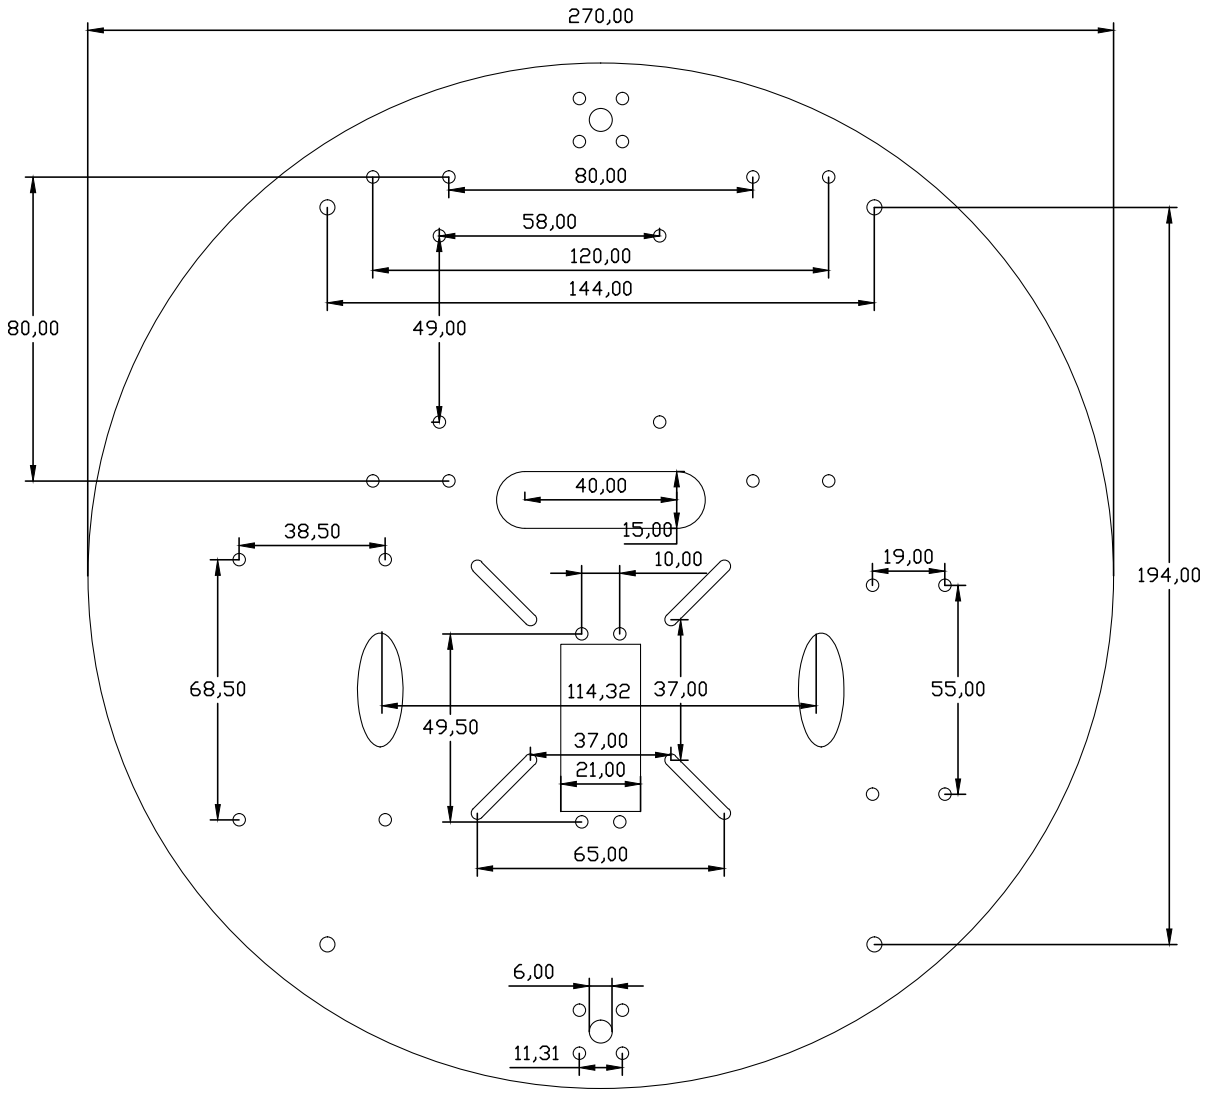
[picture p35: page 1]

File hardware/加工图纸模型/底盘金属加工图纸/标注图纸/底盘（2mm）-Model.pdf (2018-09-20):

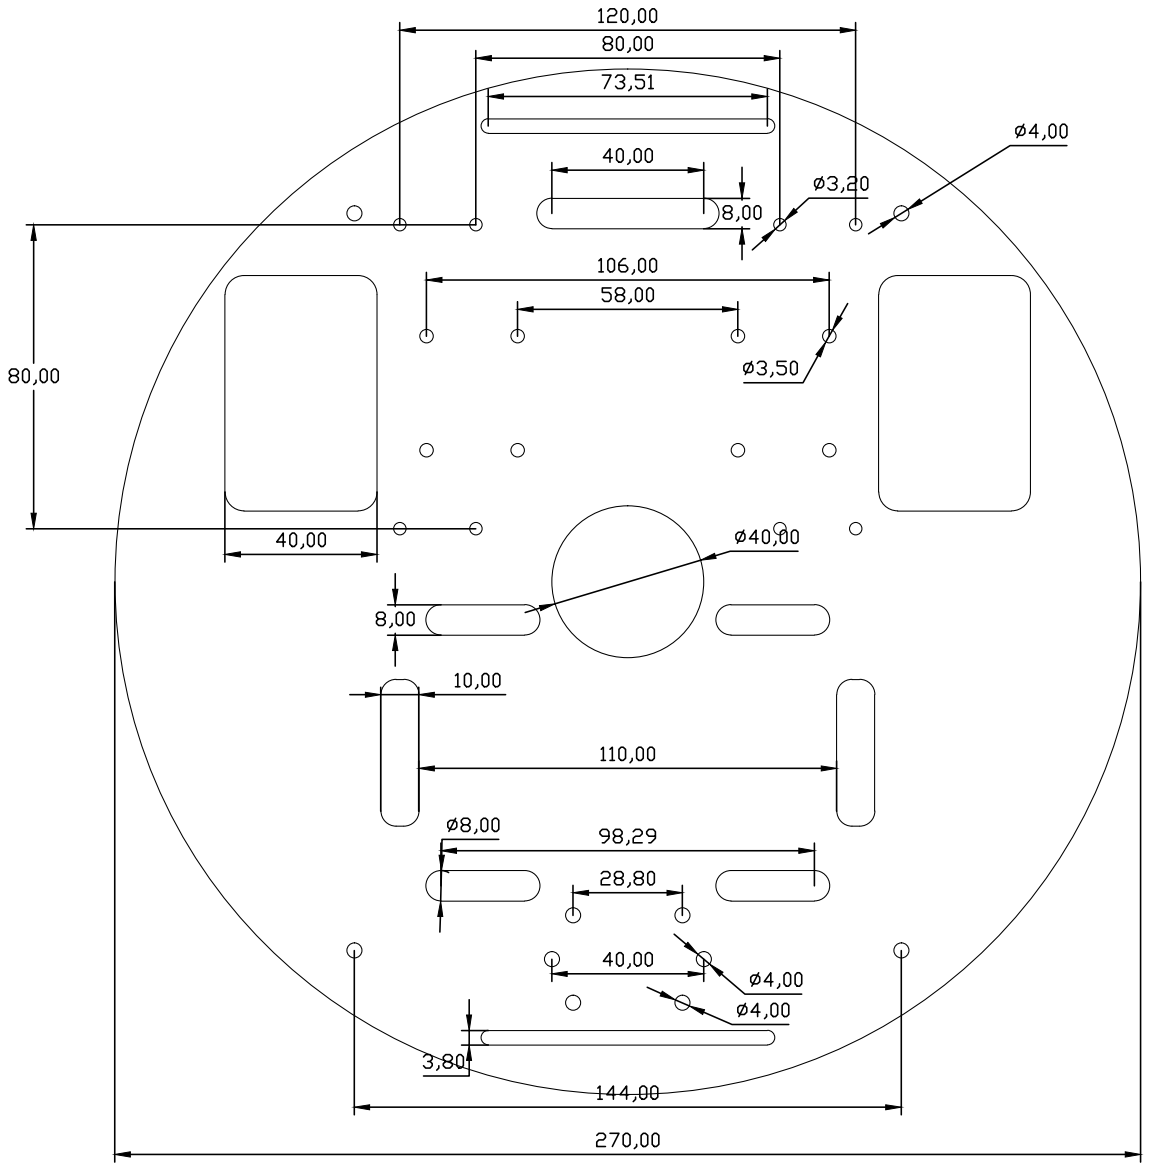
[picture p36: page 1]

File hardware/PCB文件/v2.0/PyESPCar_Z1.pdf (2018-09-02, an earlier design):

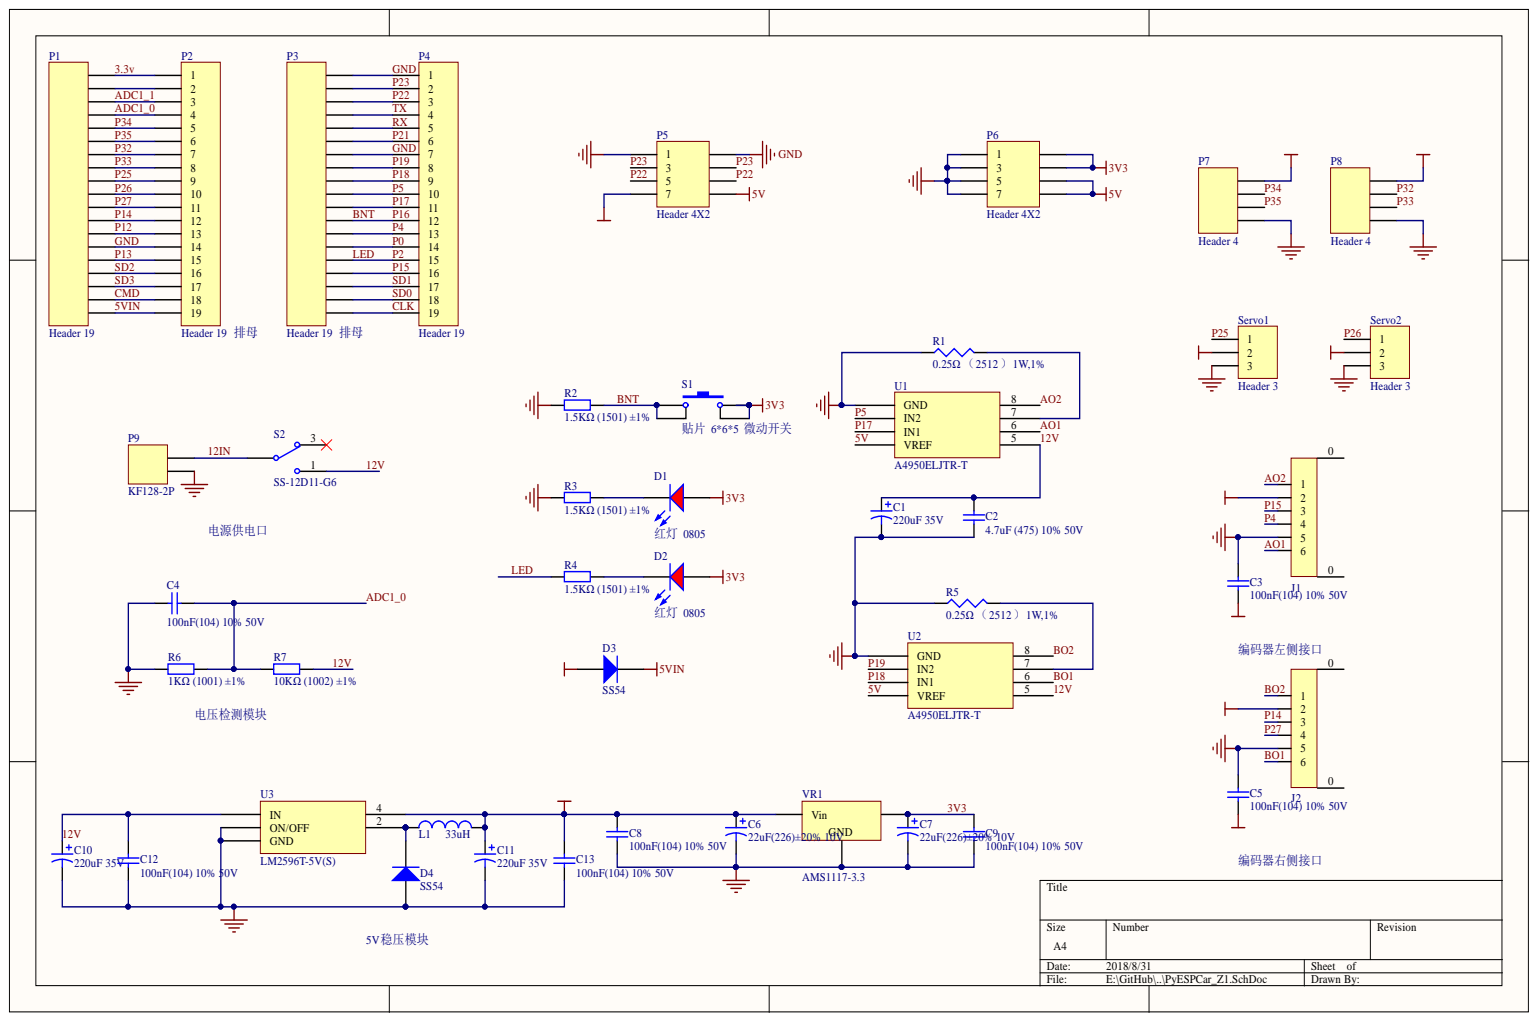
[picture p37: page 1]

12V | | L1 33uH
LM2596T-5V(S) C10

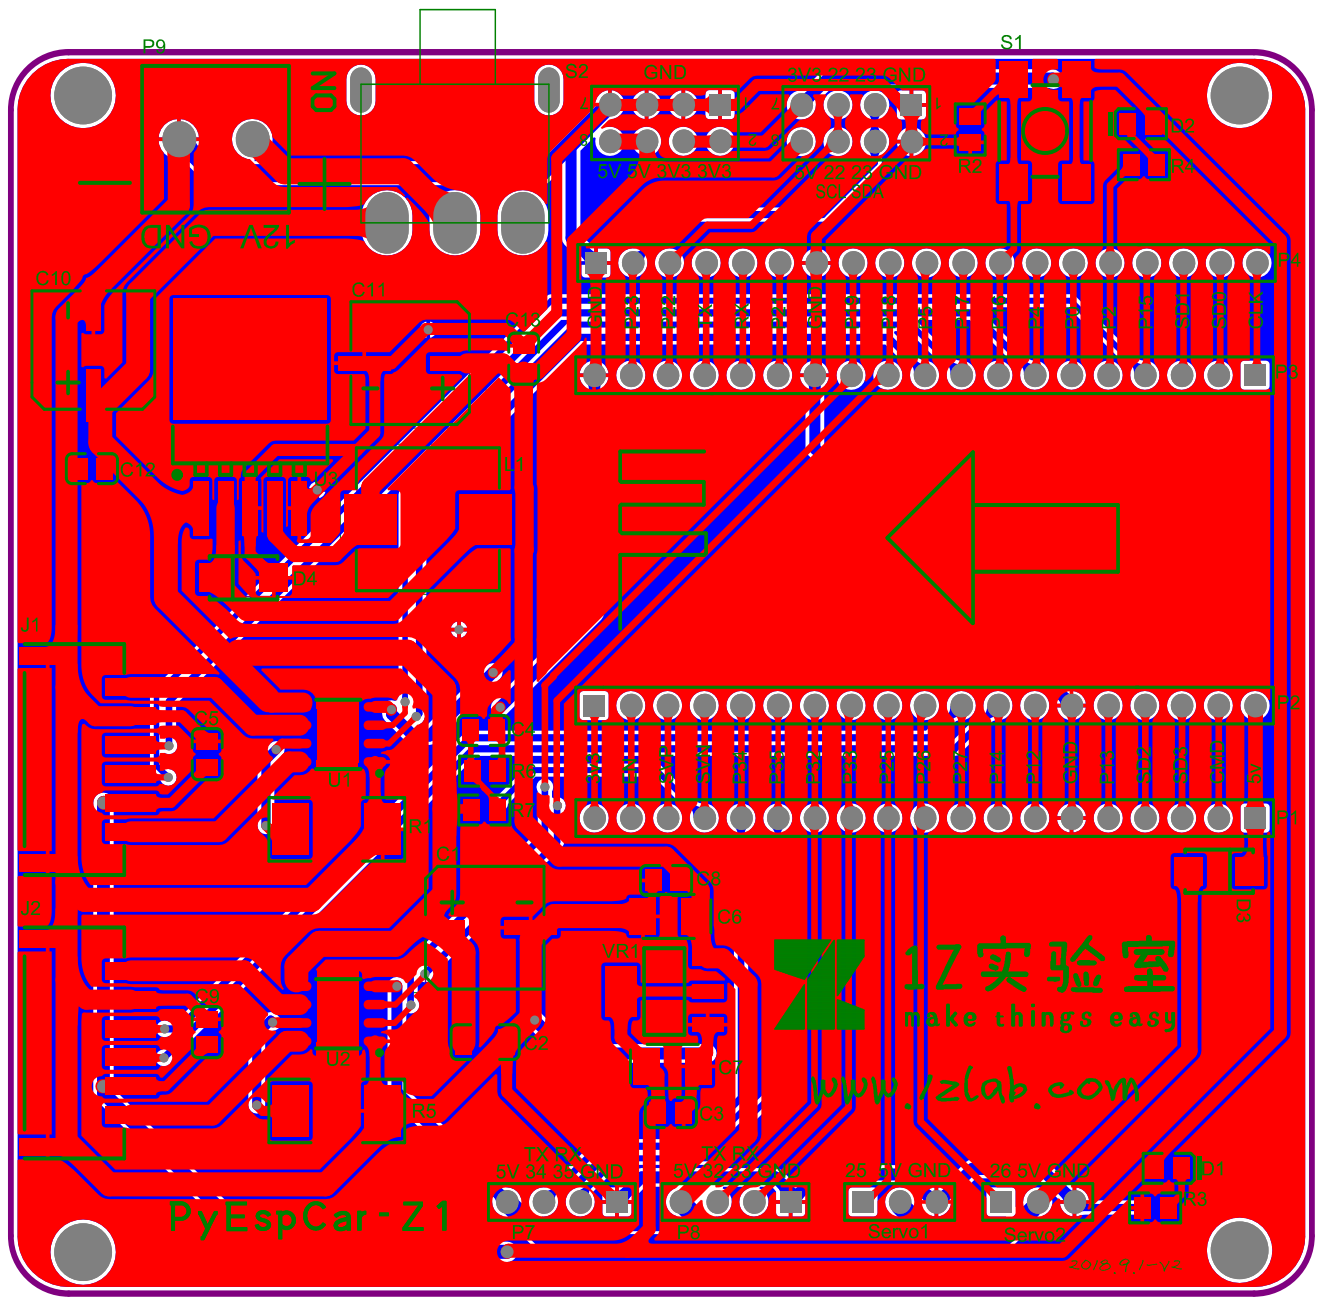
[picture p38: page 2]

Comment | Description | Designator | Footprint | LibRef | Quantity
0.25Ω （2512 ） 1W,1% | 超低阻值电阻 | R1, R5 | 2512 | Res3 | 2
1KΩ (1001) ±1% | 贴片电阻 | R6 | 0805_R | 0805 1KΩ (1001) 1% | 1
1.5KΩ (1501) ±1% | 贴片电阻 | R2, R3, R4 | 0805_R | 0603 1.5KΩ (1501) 1% | 3
4.7uF (475) 10% 50V | 贴片电容 | C2 | 1206_C | 1206 4.7uF (475) 10% 50V | 1
10KΩ (1002) ±1% | 贴片电阻 | R7 | 0805_R | 0805 1KΩ (1001) 1% | 1
22uF(226)±20% 10V | 钽电容 | C6, C7 | CAP-3528 | Cap Pol | 2
33uH ±20% | 功率电感 MS104R-330MT | L1 | CAPM100100X103 N | Inductor | 1
100nF(104) 10% 50V | 贴片电容 | C3, C4, C5, C8, C9, C12, C13 | 0805_C | 0805 100nF(104) 10% 50V | 7
220uF 35V | 贴片电解电容 , 贴片 铝解电容 , 贴片铝解 电容 | C1, C10, C11 | CAPM8485X103N | Cap Pol1 | 3
A4950ELJTR-T | A4950 电机驱动 , A4950 电机驱动 | U1, U2 | SOP-8_EP_150mil | A4950 | 2
AMS1117-3.3 | 低压差线性稳压 (LDO) | VR1 | SOT-223 | SOT-223 AMS1117-3.3 | 1
Header 3 | Header, 3-Pin | Servo1, Servo2 | HDR1X3 | Header 3 | 2
Header 4 | Header, 4-Pin | P7, P8 | HDR1X4 | Header 4 | 2
Header 4X2 | Header, 4-Pin, Dual row | P5, P6 | HDR2X4 | Header 4X2 | 2
Header 19 | Header, 19-Pin 排 针 | P1, P4 | HDR1X19 | Header 19 | 2
Header 19 排母 | Header, 19-Pin 排 母 | P2, P3 | HDR1X19 | Header 19 | 2
KF128-2P | 5.08mm 端子 | P9 | HDR2X1_D1 | Header 2 | 1
LM2596T-5V(S) | 稳压芯片 | U3 | TO-263-5 | LM2596T-5V(S) | 1
PH-PS-2.0-6 | PH-PS-2.0-6 | J1, J2 | PH-PS-2.0-6 | PH-PS-2.0-6 | 2
SS54 | 二极管 | D3, D4 | SMA(DO-214AC)_S1 | SMA(DO-214AC) SS54 | 2
SS-12D11-G6 | 拨动开关 2档带固定 脚黑色短柄 3脚侧 | S2 | SW-3 | SW-SPDT | 1
红灯 0805 | 发光二极管 | D1, D2 | 0805_LED_S1 | 0805 红灯 | 2
贴片 6*6*5 微动开关 | 贴片 6*6*5 微动开关 | S1 | SW_PB4_A1 | SW-PB4 | 1

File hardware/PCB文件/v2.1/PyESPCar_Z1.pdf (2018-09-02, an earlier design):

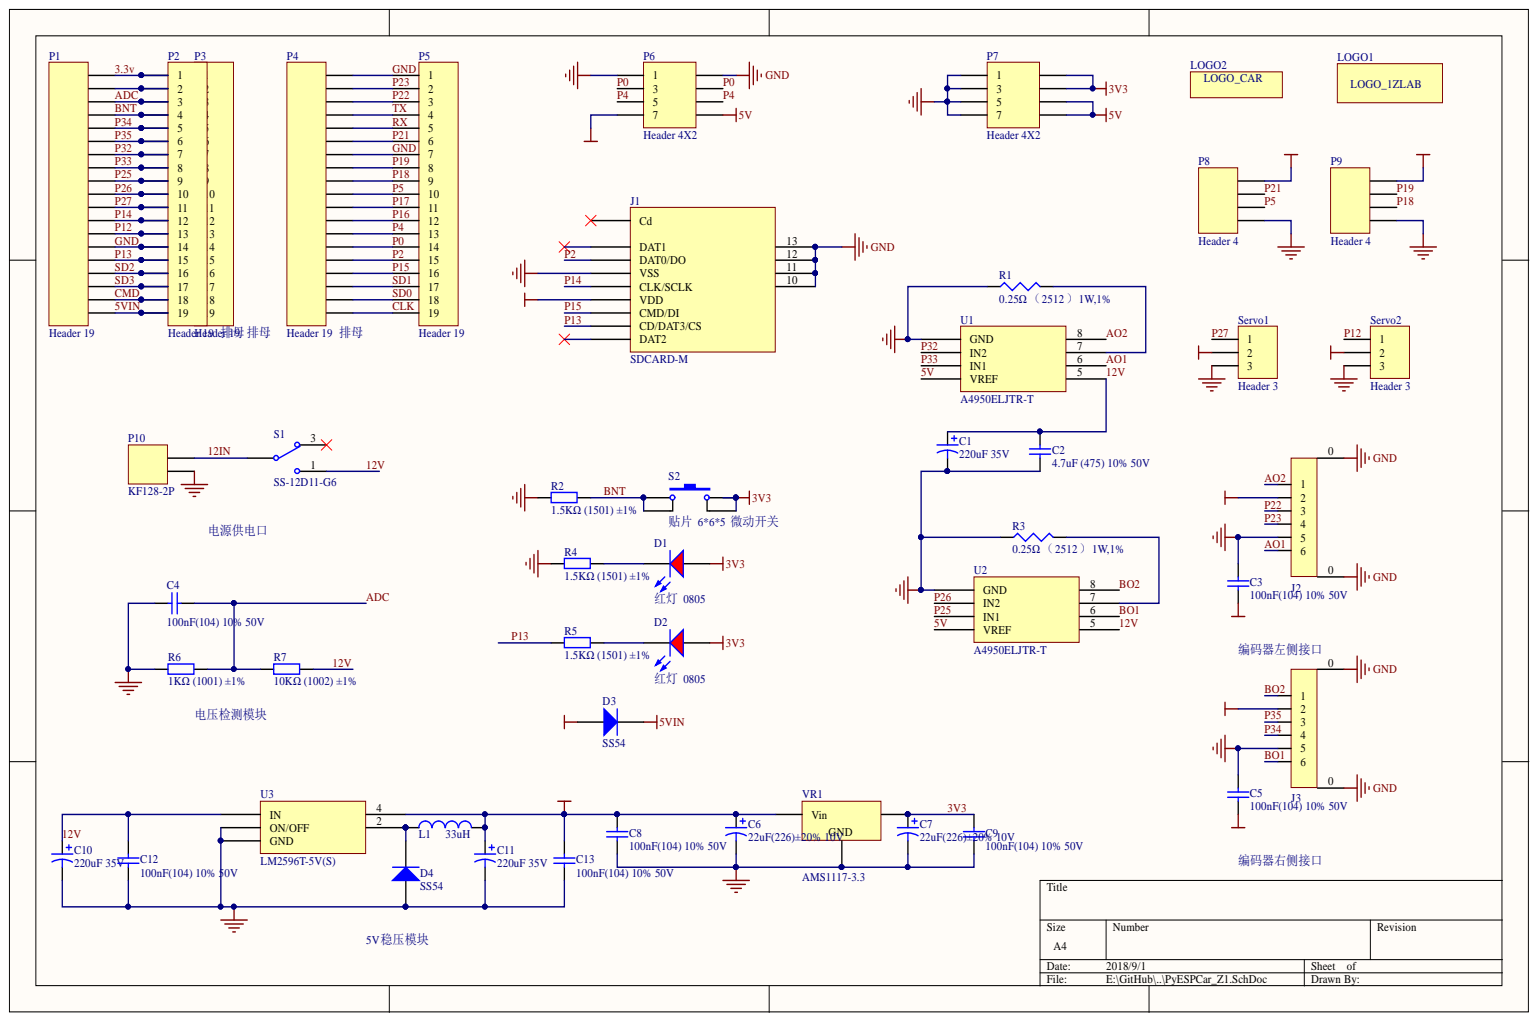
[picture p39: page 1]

12V | | L1 33uH
LM2596T-5V(S) C10

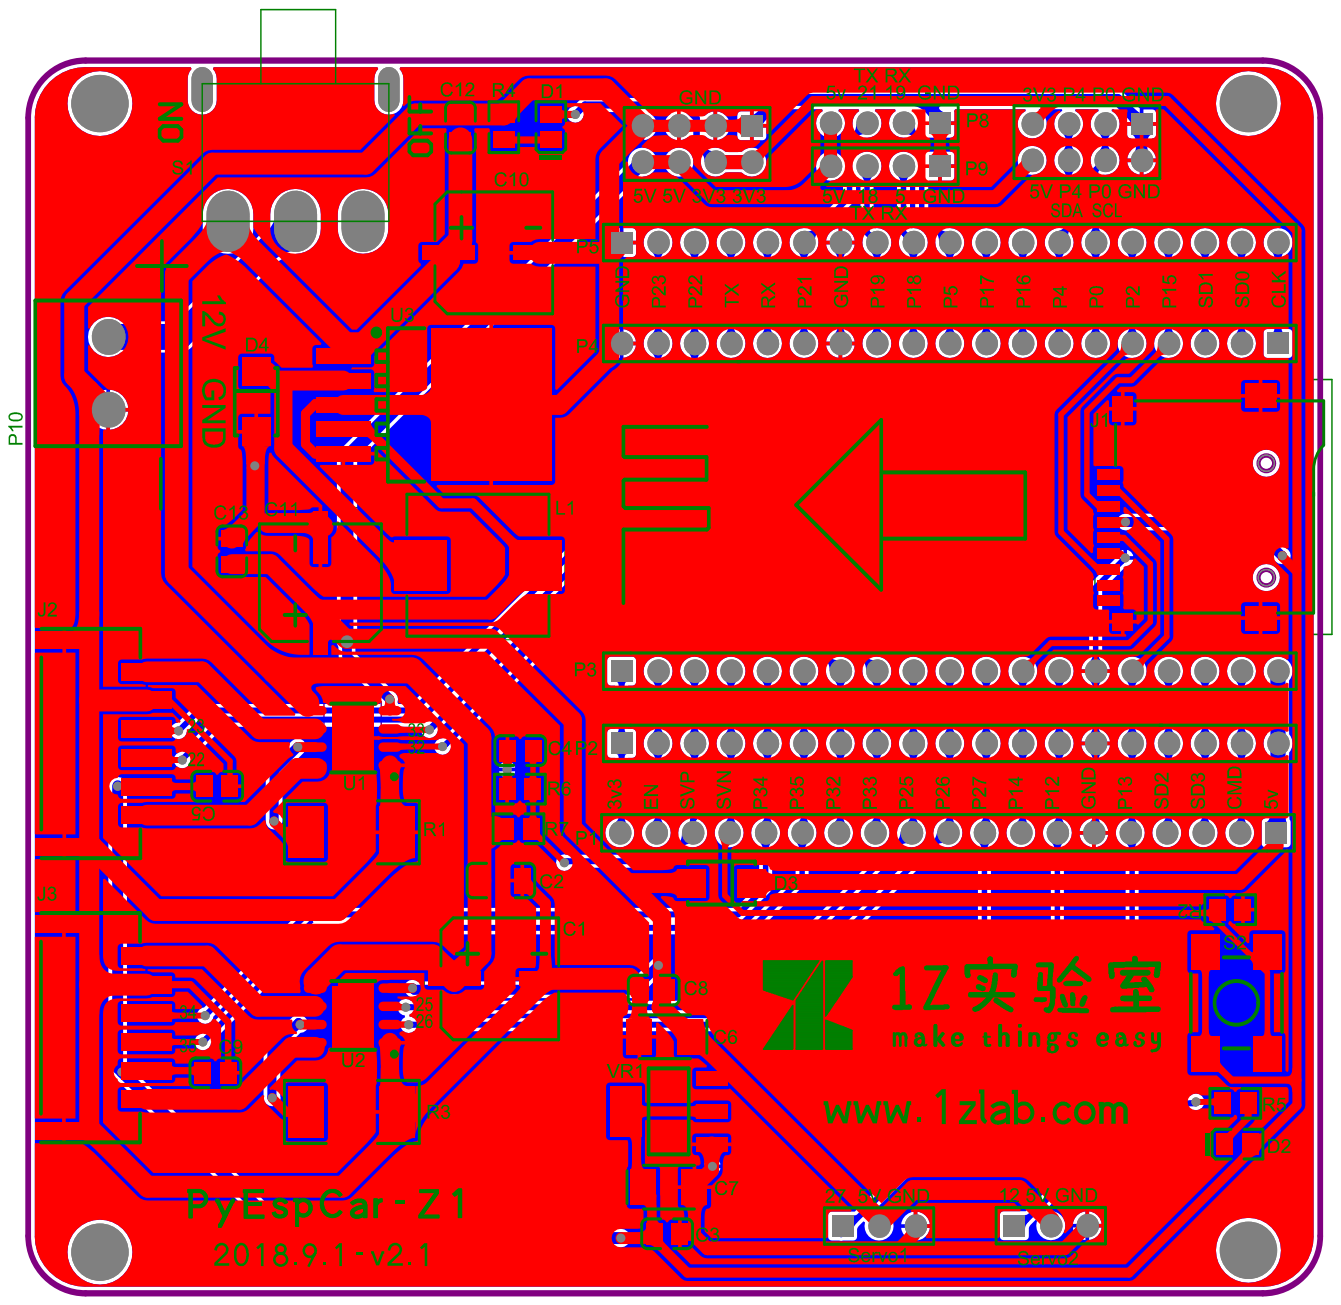
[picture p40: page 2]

Comment | Description | Designator | Footprint | LibRef | Quantity
0.25Ω （2512 ） 1W,1% | 超低阻值电阻 | R1, R3 | 2512 | Res3 | 2
1KΩ (1001) ±1% | 贴片电阻 | R6 | 0805_R | 0805 1KΩ (1001) 1% | 1
1.5KΩ (1501) ±1% | 贴片电阻 | R2, R4, R5 | 0805_R | 0603 1.5KΩ (1501) 1% | 3
4.7uF (475) 10% 50V | 贴片电容 | C2 | 1206_C | 1206 4.7uF (475) 10% 50V | 1
10KΩ (1002) ±1% | 贴片电阻 | R7 | 0805_R | 0805 1KΩ (1001) 1% | 1
22uF(226)±20% 10V | 钽电容 | C6, C7 | CAP-3528 | Cap Pol | 2
33uH ±20% | 功率电感 MS104R-330MT | L1 | CAPM100100X103 N | Inductor | 1
100nF(104) 10% 50V | 贴片电容 | C3, C4, C5, C8, C9, C12, C13 | 0805_C | 0805 100nF(104) 10% 50V | 7
220uF 35V | 贴片电解电容 , 贴片 铝解电容 , 贴片铝解 电容 | C1, C10, C11 | CAPM8485X103N | Cap Pol1 | 3
A4950ELJTR-T | A4950 电机驱动 , A4950 电机驱动 | U1, U2 | SOP-8_EP_150mil | A4950 | 2
AMS1117-3.3 | 低压差线性稳压 (LDO) | VR1 | SOT-223 | SOT-223 AMS1117-3.3 | 1
Header 3 | Header, 3-Pin | Servo1, Servo2 | HDR1X3 | Header 3 | 2
Header 4 | Header, 4-Pin | P8, P9 | HDR1X4 | Header 4 | 2
Header 4X2 | Header, 4-Pin, Dual row | P6, P7 | HDR2X4 | Header 4X2 | 2
Header 19 | Header, 19-Pin 排 针 | P1, P5 | HDR1X19 | Header 19 | 2
Header 19 排母 | Header, 19-Pin 排 母 | P2, P3, P4 | HDR1X19 | Header 19 | 3
KF128-2P | 5.08mm 端子 | P10 | HDR2X1_D1 | Header 2 | 1
LM2596T-5V(S) | 稳压芯片 | U3 | TO-263-5 | LM2596T-5V(S) | 1
LOGO_1ZLAB | | LOGO1 | 1ZLAB_LOGO | LOGO_1ZLAB | 1
LOGO_CAR | | LOGO2 | car_logo | LOGO_CAR | 1
PH-PS-2.0-6 | PH-PS-2.0-6 | J2, J3 | PH-PS-2.0-6 | PH-PS-2.0-6 | 2
SDCARD-M | TF卡槽 | J1 | SDCARD-M | SDCARD-M | 1
SS54 | 二极管 | D3, D4 | SMA(DO-214AC)_S1 | SMA(DO-214AC) SS54 | 2
SS-12D11-G6 | 拨动开关 2档带固定 脚黑色短柄 3脚侧 | S1 | SW-3 | SW-SPDT | 1
红灯 0805 | 发光二极管 | D1, D2 | 0805_LED_S1 | 0805 红灯 | 2
贴片 6*6*5 微动开关 | 贴片 6*6*5 微动开关 | S2 | SW_PB4_A1 | SW-PB4 | 1

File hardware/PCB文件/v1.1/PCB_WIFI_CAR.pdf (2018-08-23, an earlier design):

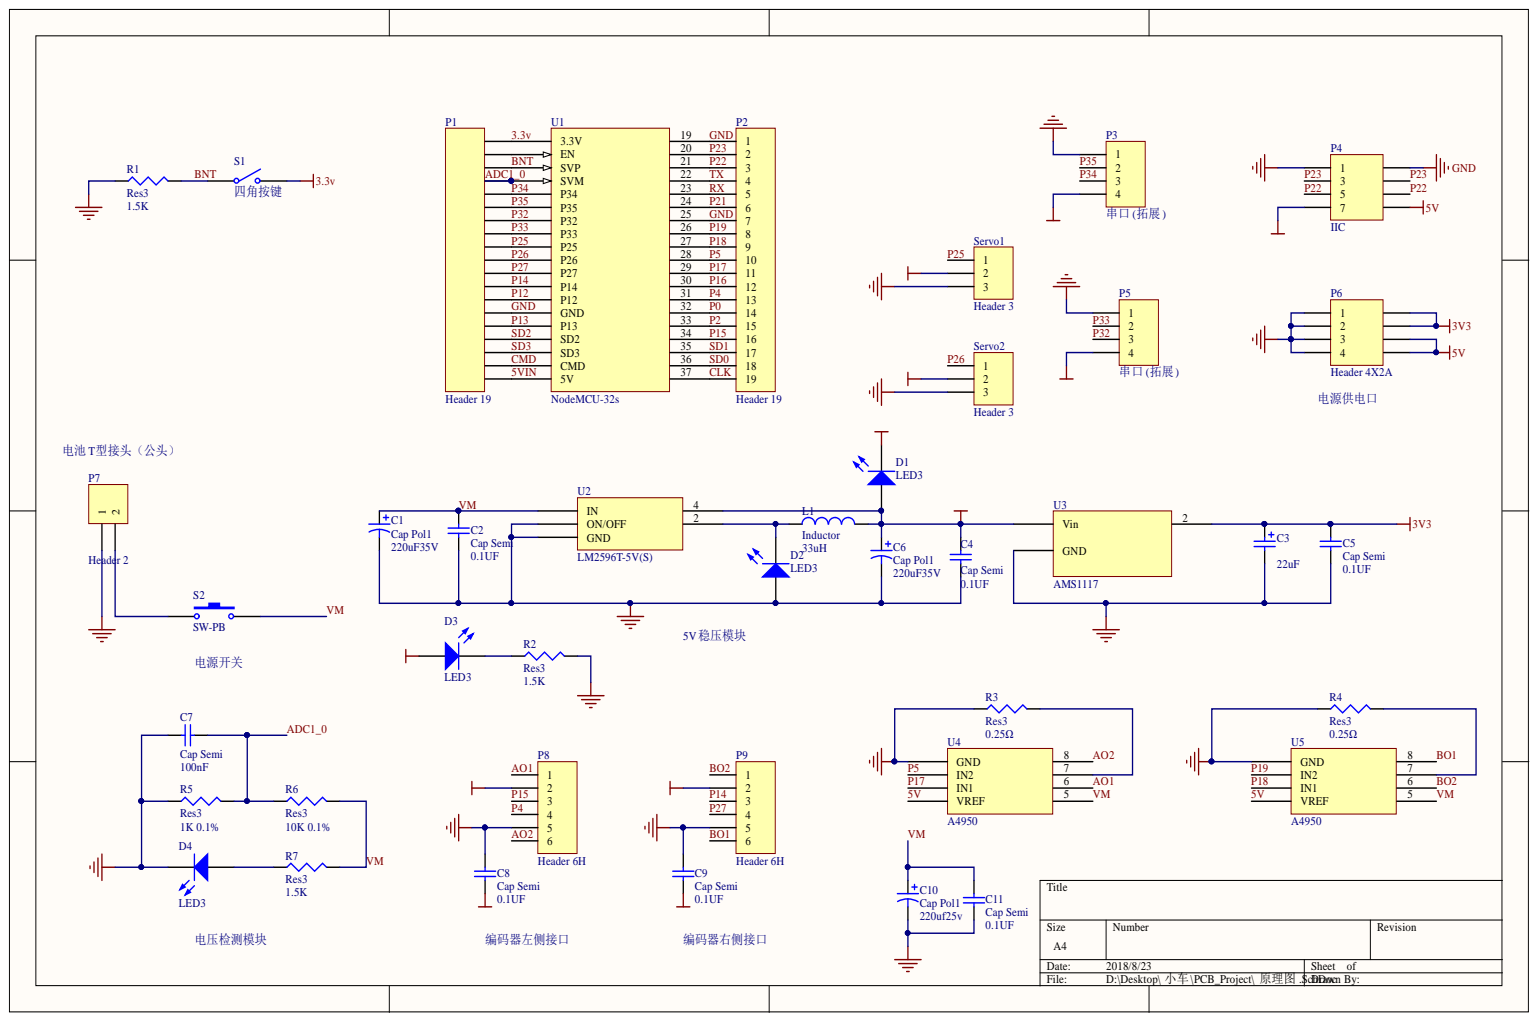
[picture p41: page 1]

P35 | P21
P32 | GND
P33 | P19
P25 | P18

P27 | P17
P14 | P16
P12 | P4

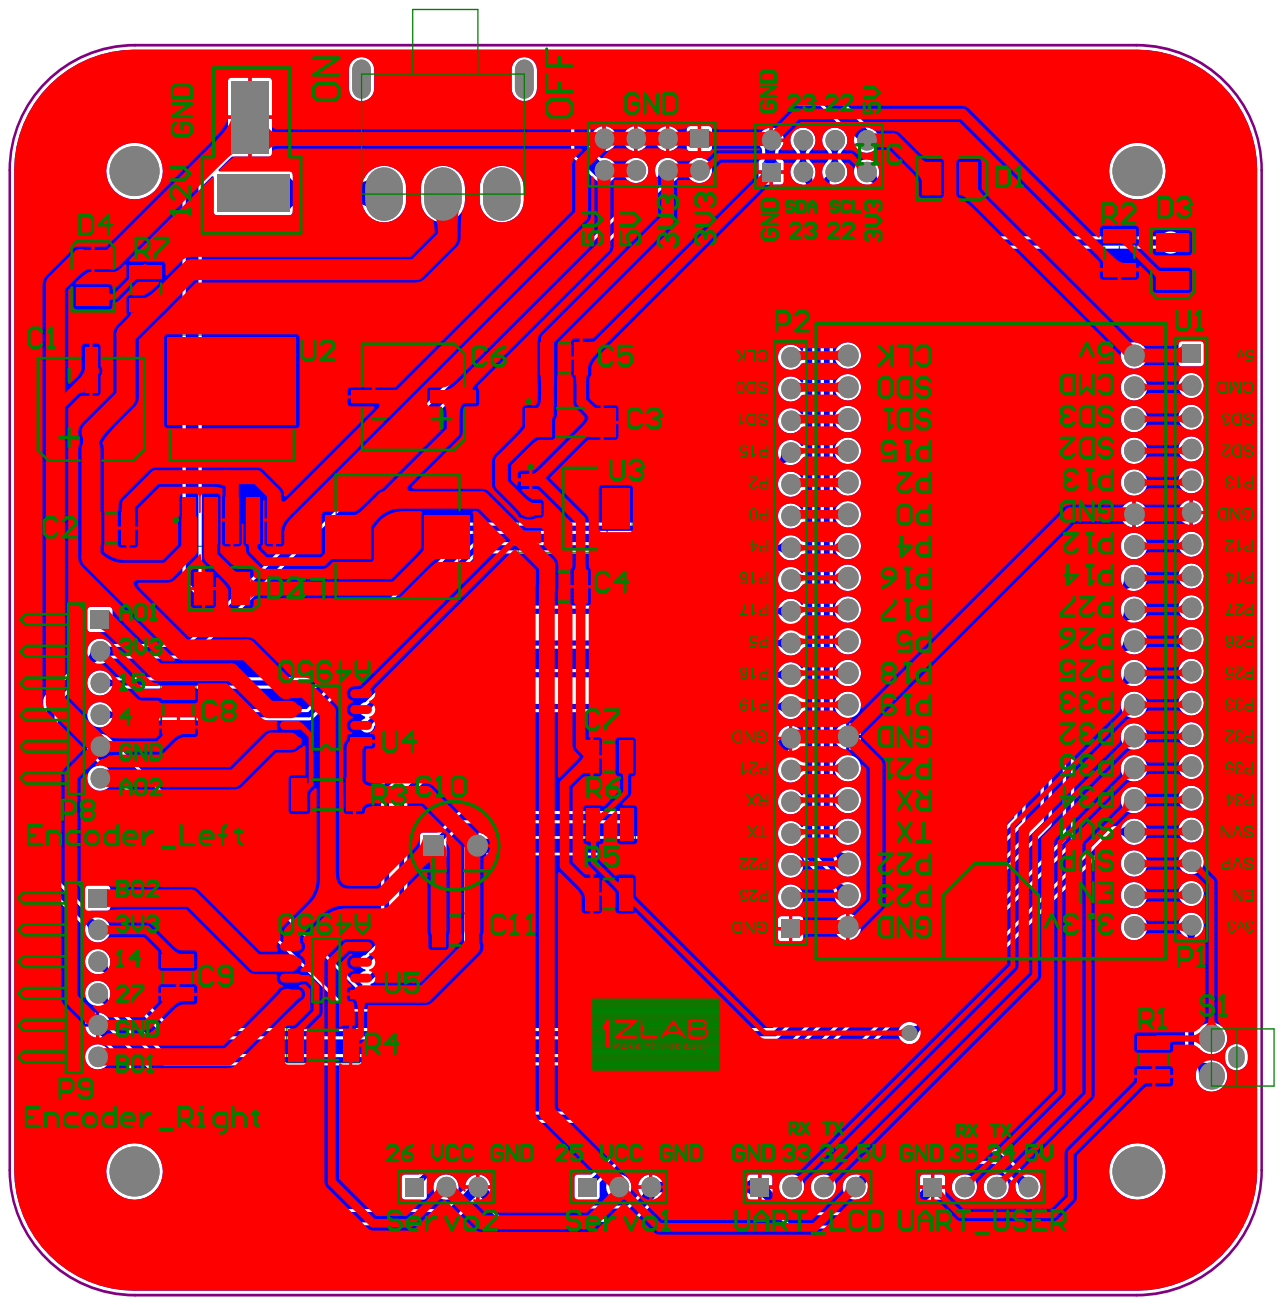
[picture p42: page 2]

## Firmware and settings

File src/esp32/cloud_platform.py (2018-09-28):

# -*- coding:utf-8 -*-
'''
基于PCA9685 I2C舵机控制模块对舵机进行控制的库

上臂舵机 控制精度: 0.45度
下臂舵机 控制精度: 0.63度
'''
import pca9685
import math
from car_config import car_property

class Servo:
    '''
    利用PCA9685控制Servo
    '''
    def __init__(self, pca9685, servo_idx, min_duty=30, max_duty=130, angle_range=180, default_angle=90):
        '''
        Servo的构造器
        '''
        # PCA9685舵机驱动板
        self.pca9685 = pca9685
        # 舵机在PCA9695舵机驱动板上的编号
        self.servo_idx = servo_idx
        # 舵机最小角度时候的占空比
        self.min_duty = min_duty
        # 舵机最大角度时候的占空比
        self.max_duty = max_duty
        # 舵机角度范围
        self.angle_range = angle_range
        # 舵机默认角度
        self.default_angle = default_angle
        # 当前的角度值
        self._angle = default_angle
        # 舵机旋转到默认的角度
        self.angle(default_angle)
        

    def _angle2duty(self, angle):
        duty = self.min_duty + (self.max_duty - self.min_duty)*( angle / self.angle_range)
        return int(duty)

    def angle(self, value=None):
        if value is None:
            # 返回当前舵机的角度
            return self._angle
        else:
            value = float(value)
            # 计算舵机的占空比
            duty = self._angle2duty(value)
            # 执行指令
            self.pca9685.duty(self.servo_idx, duty)
            # 更新当前的角度值
            self._angle = value
    
    def reset(self):
        self.angle(self.default_angle)

class CloudPlatform:
    '''
    舵机云台
    PCA9685的Duty取值范围为 0- 4095
    '''
    def __init__(self, i2c, address=0x40, freq=50):
        # 创建PCA9685对象
        self.pca9685 = pca9685.PCA9685(i2c, address)
        # 设定PWM的频率
        self.pca9685.freq(freq)

        self.bottom_servo = Servo(
            self.pca9685,
            car_property['BOTTOM_SERVO_IDX'],
            min_duty=car_property['BOTTOM_SERVO_MIN_DUTY'],
            max_duty=car_property['BOTTOM_SERVO_MAX_DUTY'],
            angle_range=car_property['BOTTOM_SERVO_ANGLE_RANGE'],
            default_angle=car_property['BOTTOM_SERVO_DEFAULT_ANGLE'])
        
        self.top_servo = Servo(
            self.pca9685,
            car_property['TOP_SERVO_IDX'],
            min_duty=car_property['TOP_SERVO_MIN_DUTY'],
            max_duty=car_property['TOP_SERVO_MAX_DUTY'],
            angle_range=car_property['TOP_SERVO_ANGLE_RANGE'],
            default_angle=car_property['TOP_SERVO_DEFAULT_ANGLE'])
    
    def down(self, delta_angle=5):
        '''
        云台上臂向下
        '''
        delta_angle = float(delta_angle)

        cur_angle = self.top_servo.angle()
        target_angle = cur_angle - delta_angle

        if target_angle >= 0:
            self.top_servo.angle(target_angle)
    
    def up(self, delta_angle=5):
        '''
        云台上臂向上
        '''
        delta_angle = float(delta_angle)

        cur_angle = self.top_servo.angle()
        target_angle = cur_angle + delta_angle

        if target_angle <= self.top_servo.angle_range:
            self.top_servo.angle(target_angle)
    
    def left(self, delta_angle=5):
        '''
        云台下臂向左
        '''
        delta_angle = float(delta_angle)

        cur_angle = self.bottom_servo.angle()
        target_angle = cur_angle + delta_angle

        if target_angle <= self.bottom_servo.angle_range:
            self.bottom_servo.angle(target_angle)
            
    def right(self, delta_angle=5):
        '''
        云台下臂向右
        '''
        delta_angle = float(delta_angle)
        
        cur_angle = self.bottom_servo.angle()
        target_angle = cur_angle - delta_angle

        if target_angle >= 0:
            self.bottom_servo.angle(target_angle)
    
    def reset(self):
        
        self.top_servo.reset()
        self.bottom_servo.reset()

if __name__ == '__main__':
    '''
    测试舵机云台
    '''
    from machine import I2C,Pin
    from car_config import gpio_dict, car_property
    # from cloud_platform import CloudPlatform

    # 创建一个I2C对象
    i2c = I2C(
        scl=Pin(gpio_dict['I2C_SCL']),
        sda=Pin(gpio_dict['I2C_SDA']),
        freq=car_property['I2C_FREQUENCY'])

    # 创建云台对象
    cp = CloudPlatform(i2c)

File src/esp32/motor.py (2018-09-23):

'''
电机控制类
'''
from machine import Pin,PWM
from car_config import car_property,gpio_dict

class Motor:
    # MOTOR列表
    MOTOR_LIST = [
        (
            gpio_dict['LEFT_MOTOR_A'],
            gpio_dict['LEFT_MOTOR_B'],
            car_property['LEFT_MOTOR_INSTALL_DIR']
        ),
        (
            gpio_dict['RIGHT_MOTOR_A'],
            gpio_dict['RIGHT_MOTOR_B'],
            car_property['RIGHT_MOTOR_INSTALL_DIR']
        )
    ]

    # 电机的PWM频率还有PWM取值范围
    MOTOR_MAX_PWM = car_property['MOTOR_MAX_PWM']
    MOTOR_PWM_FREQUENCY = car_property['MOTOR_PWM_FREQUENCY']

    def __init__(self, idx, is_debug=False):
        
        gpio_a, gpio_b, self.motor_install_dir = Motor.MOTOR_LIST[idx]
        # A相PWM
        self.pwm_a = PWM(
            Pin(gpio_a, Pin.OUT),
            freq = Motor.MOTOR_PWM_FREQUENCY,
            duty = 0)
        
        # B相PWM
        self.pwm_b = PWM(
            Pin(gpio_b, Pin.OUT),
            freq = Motor.MOTOR_PWM_FREQUENCY,
            duty = 0)
        
        # 电机安装方向
        if not self.motor_install_dir:
            self.pwm_a, self.pwm_b = self.pwm_b, self.pwm_a
        
        # 电机速度信号 取值范围: -1023 - 1023 
        self._pwm = 0
        # 设置电机的PWM
        # self.pwm(self._pwm)
    
    def stop(self):
        '''
        电机停止转动
        '''
        self.speed = 0
    
    @property
    def speed(self):
        return self._pwm

    @speed.setter
    def speed(self, value):
        value = int(value)
        if abs(value) > Motor.MOTOR_MAX_PWM:
            # 判断pwm的绝对值是否越界
            value = Motor.MOTOR_MAX_PWM if value > 0 else -1*Motor.MOTOR_MAX_PWM
        
        # 设置当前的PWM信号
        self._pwm = value
        # 驱动电机驱动
        if self._pwm >= 0:
            self.pwm_a.duty(0)
            self.pwm_b.duty(abs(self._pwm))
        else:
            self.pwm_a.duty(abs(self._pwm))
            self.pwm_b.duty(0)

    @property
    def speed_percent(self):
        '''获得百分比标识的小车'''
        return (self.speed / 1023) * 100

    @speed_percent.setter
    def speed_percent(self, value):
        speed = int(value / 100 * 1023)
        self.speed = speed
        
    def deinit(self):
        '''
        资源释放
        '''
        # pwm资源释放
        self.pwm_a.deinit()
        self.pwm_b.deinit()
    

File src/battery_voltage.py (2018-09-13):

'''
对电池电压进行采样
-------------------
航模电池需要监控电池的电压
满电或者过放都不好,需要检测电压值是否低于某个特定的值, 
如果低于的话, 电机停止工作.
'''
from machine import Pin,Timer,ADC
import utime

class BatteryVoltage(object):
    
    def __init__(self, gpio_id, is_debug=False):
        self.BV_SAMPLE_PERIOD = 100 # 采样周期(次数)为2000次
        self.OVER_DISCHARGE_VOLTAGE = 6.4 # 过放电压参考值
        self.pin = Pin(gpio_id, Pin.IN) # 电压采样引脚
        self.adc = ADC(self.pin) # 创建引脚对应的ADC对象
        self.init_adc() # 初始化ADC
        
        self.bv_sample_cnt = 0 # 统计次数
        self.bv_sample_sum = 0 # 采样电压总和
        self.battery_voltage = 0 # 电池电压 
        # 初始化电池电压
        self.init_battery_voltage()
        # 创建一个定时器
        # self.timer = Timer(timer_id) 
        # 每隔1ms执行一次
        # self.timer.init(period=1, mode=Timer.PERIODIC, callback=self.callback)
        # 电池是否过放
        self.is_over_discharge = False # 电池是否过放
        # 是否开启调试模式
        self.is_debug = is_debug
    def init_adc(self):
        '''
        初始化ADC
        '''
        # 设定满量程为 3.3v
        self.adc.atten(ADC.ATTN_11DB)
        # 设定取值范围在0-1023
        self.adc.width(ADC.WIDTH_10BIT)
    
    def init_battery_voltage(self):
        '''
        初始化，电池电压
        '''
        # 采样BV_SAMPLE_PERIOD次
        for i in range(self.BV_SAMPLE_PERIOD):
            self.bv_sample_sum += self.adc.read()
        # 更新电池电压
        self.battery_voltage = self.adc2volt(self.bv_sample_sum/self.BV_SAMPLE_PERIOD)
        # 累加值清零
        self.bv_sample_sum = 0

    def callback(self, timer):
        '''
        定时器回调函数
        '''
        self.bv_sample_cnt += 1 # 计数器自增
        # 采样电池，并累加
        self.bv_sample_sum += self.adc.read()

        if self.bv_sample_cnt >= self.BV_SAMPLE_PERIOD:
            # 判断是否满足周期
            self.battery_voltage = self.adc2volt(self.bv_sample_sum/self.BV_SAMPLE_PERIOD)
            if self.battery_voltage < self.OVER_DISCHARGE_VOLTAGE:
                # 电压低于过放电压
                self.is_over_discharge = True
            else:
                self.is_over_discharge = False
            
            # 清零
            self.bv_sample_cnt = 0
            self.bv_sample_sum = 0
            # 打印电池电压Debug信息
            if self.is_debug:
                print("Battery Voltage: {}".format(self.battery_voltage))
                
    @staticmethod
    def adc2volt(value, scaler=11):
        '''
        将ADC采样值（0-1024）转换为实际的电压
        @scalar scalar为放缩因子，取决与电路电阻分压
        '''
        return value / 1024 * 3.3 * scaler

    def deinit(self):
        '''
        释放资源
        备注 ADC没有deinit方法
        '''
        # 释放ADC资源
        # self.adc.deinit()
        pass


if __name__ == '__main__':
    '''
    测量电池电压
    '''
    from car_config import gpio_dict
    # from battery_voltage import BatteryVoltage
    from machine import Timer

    bv = BatteryVoltage(gpio_dict['BATTERY_ADC'], is_debug=True)
    # 创建一个定时器
    timer = Timer(1) 
    # 每隔100ms执行一次 10s 判断一次电池电压是否过放
    timer.init(period=100, mode=Timer.PERIODIC, callback=bv.callback)

    try:
        while True:
            pass
    except:
        # 释放定时器资源
        timer.deinit()
        # 释放ADC资源
        bv.deinit()

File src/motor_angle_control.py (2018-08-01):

from machine import Timer
from pid import PID

class MotorAngleControl(object):
    '''
    电机的角度控制PID
    使用PID，结合编码器提供的反馈
    每隔100ms采样一次
    '''
    def __init__(self, motor, encoder, kp, ki=0, kd=0, is_debug=False):
        # 电机对象
        self.motor = motor
        # 编码器
        self.encoder = encoder
        # 角度与编码器计数之间的缩放因子
        self.scalar = 1
        # PID对象
        self.pid = PID(kp, ki, kd)
        # 创建定时器
        self.timer = Timer(4)
        # 设置定时器回调 100ms执行一次
        self.timer.init(period=100, mode=Timer.PERIODIC, callback=self.callback)
        # 是否重置计数器
        self.is_reset = False
        
    def count2angle(self, count):
        '''
        将编码器计数转换为角度
        '''
        return count * self.scalar

    def angle2count(angle):
        '''
        将角度转换为编码器计数
        '''
        return angle / self.scalar

    def set_angle(self, angle, is_reset=False):
        '''
        设置电机的旋转角度
        @angle:  电机旋转角度
        @is_continue: 电机是否重新复位
            * False: 不复位的话，计数器不清，
                0度在编码器最初始的位置 
            * True: 如果连续旋转，旋转到特定角度的话，
                编码器计数清零， 目标角度设定为0度,同时is_reset=False
        '''
        self.is_reset = is_reset
        # 设定目标计数
        target_count = self.angle2count(angle)
        if is_reset:
            # 计数器清零
            self.encoder.count = 0
        else:
            # 目标计数器加上之前编码器的值
            target_count += self.encoder.count
        
        # 设置PID的目标取值
        self.pid.set_target_value(target_count)

    def callback(self, timer):
        '''
        回调函数
        '''
        # 获取当前编码器的真实取值
        real_value = self.encoder.count
        # 更新PID
        result = self.pid.update(real_value)
        if self.is_debug:
            print("Target: {} RealValue: {} PID Result: {}".format(self.pid.target_value, self.motor.count, result))
        # 将result转换为电机转速
        pwm = 1*result
        # pwm的值放缩在 正负250-1023之间
        self.motor.set_pwm(pwm)
        
class MotorSpeedPID(object):
    def __init__(self, motor, encoder):
        pass
        

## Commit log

2018-07-30 update encoder
2018-07-30 add 管脚接线Table
2018-07-30 添加README中的内容
2018-07-30 添加了电池电压采样，用户按键，电机控制的源码
2018-07-31 添加并测试完成encoder模块
2018-07-31 remove 测试代码
2018-07-31 创建文档doc文件夹
2018-08-01 调整文档
2018-08-17 解决编码器的问题
2018-08-19 PID角度控制基本完成
2018-08-19 update README 添加项目贡献者
2018-08-19 完善硬件部分
    整理了一下小车机械部分，3D建模软件使用SolidWorks2016
    [DS3119MG.SLDPRT, 中间板.SLDPRT, 中间板（2mm铝合金）（改）.DWG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]
2018-08-20 修改小峰主页地址
2018-08-20 添加零件图片，删除无用零件
    [DS3119MG.SLDPRT, 云台 - 轴-2.STL, 云台 - 轴承座-2.STL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]
2018-08-20 添加软件说明
2018-08-20 更新了硬件README
2018-08-20 update README 更新推广图，添加硬件资料入口
2018-08-20 添加1Z实验室介绍
2018-08-21 添加网友写的编码器解码程序
2018-08-21 修改src/encoder文件夹下内容
2018-08-21 整理程序 src\encoder\encoder_test.py
2018-08-22 编码器测试 完美 小峰棒棒的
2018-08-22 修改编码器测试代码，减少print次数
2018-08-22 添加编码器测试的注释
2018-08-22 完成电机角度PID控制
2018-08-22 添加右侧电机的PID角度控制，添加PID参数到 car_config
2018-08-23 添加PCB
    [PCB_Project.PrjPcb, lib_all.SchLib, lib_pcb_all.PcbLib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]
2018-08-23 添加PCB文件PDF
2018-08-23 添加小车详细介绍
2018-08-23 更新小车底板的照片
2018-08-23 修改小车模型
    [PCB尺寸.DWG, 中间板.SLDPRT, 中间板（2mm铝合金）（改）.DWG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]
2018-08-23 修正图纸
    [中间板.SLDPRT, 中间板（2mm）-v.DWG, 云台.SLDASM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]
2018-08-23 修改小车图片
2018-08-23 修改图片
2018-08-25 完成PID可视化调试工具 串口通信部分
2018-08-25 修改云台尺寸
    [云台 - DS3119MG-2.STL, 云台 - DS3119MG-3.STL, 云台 - deep groove ball bearings gb-1.STL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]
2018-08-25 修改ADC引脚
2018-08-25 修改电池测试
2018-08-25 添加测试销毁函数
2018-08-25 添加一些资源释放的代码
2018-08-26 增加PCB版本
    [PCB尺寸.DWG, PyESPCar_Z1.PcbDoc, PyESPCar_Z1.PrjPcb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]
2018-08-26 添加代码注释
2018-08-26 添加物料核算清单
2018-08-27 完善2.0PCB
    [DS3119MG.SLDPRT, PCB1.PcbDoc, PyESPCar_Z1.CSV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]
2018-08-27 修改学校
2018-08-27 延->彦
2018-08-30 update 报价单
2018-08-30 修改PCB
    [DS3119MG.SLDPRT, PCB1.PcbDoc, PyESPCar_Z1.PrjPcb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]
2018-08-31 添加配件爆炸图
2018-08-31 提交servo.py
2018-09-01 修改引脚
    [PCB尺寸.DWG, PyESPCar_Z1.PcbLib, PyESPCar_Z1.PrjPcb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]
2018-09-01 删除无效文件
    [PCB尺寸.DWG, PyESPCar_Z1.CSV, PyESPCar_Z1.xlsx]
2018-09-02 添加小车所用芯片资料
2018-09-02 添加servo与pid速度控制 待测试
2018-09-03 添加积分上限，重新修订PID参数
2018-09-05 添加PID速度控制，但是速度大于55之后存在周期性震荡的问题
2018-09-06 封装了串口调试类, PID重新调参, 小车限速
2018-09-06 添加旋转角度控制, (需要乘比例系数版本)
2018-09-07 添加左右两个轮子同步的代码
2018-09-10 添加move功能(需更新控制方式, 改用速度积分), 修改car_config
2018-09-10 修改car_config
2018-09-10 修改云台定位孔
    [DS3119MG.SLDPRT, PCB尺寸.DWG, PyESPCar_Z1.PcbLib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]
2018-09-11 改用舵机控制板,控制舵机
2018-09-11 添加位姿积分
2018-09-12 运动学控制模型不全面,暂时屏蔽了位姿推导
2018-09-12 添加转向,前进后退的功能
2018-09-12 完成位姿推导, 可以实现比较精确的前进与转角检测
2018-09-12 添加舵机云台的基本控制 上下左右
2018-09-13 添加串口液晶屏
2018-09-13 添加螺丝铜柱零配件清单
2018-09-14 更新README 实物图配图
2018-09-14 更新README 实物图路径
2018-09-15 改正近期发现的问题
    [DS3119MG.SLDPRT, deep groove ball bearings gb.sldprt, 中间板.SLDPRT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]
2018-09-15 添加图纸标注
    [DIN 967 - M4 x 6 - Z --- 4.6S.sldprt, PyESPCar_Z1.PrjPcb, PyESPCar_Z1.SchDoc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]
2018-09-17 重新整理文件夹，移除libs
2018-09-19 解决走直线的难题
2018-09-20 更新了motor还有encoder的api
2018-09-21 移植到Tpyboard
2018-09-21 添加ADC采样
2018-09-21 PyBoard添加电机PID速度控制部分
2018-09-22 删减PyESPCar的功能
2018-09-22 remove stm32 code for empcar
2018-09-22 更新README.md, 因为ESP32硬件局限所以对功能做了取舍
2018-09-23 更新了简约版的config文件
2018-09-23 添加mqtt协议，键盘事件监听控制小车
2018-09-23 修改程序入口
2018-09-26 移除boot.py
2018-09-28 去除main中自动运行 mqtt的代码
2018-09-28 提交色块追踪的草稿
2018-09-28 提交不稳定的小车追踪02
2018-09-29 完善色块追踪功能
2018-10-02 update 色块追踪
2018-10-02 完成色块追踪(待重构)
2018-10-02 修改语言attri
2018-10-04 综合例程移动Example文件夹下
2018-10-04 完善色块追踪小车的代码
2018-10-04 添加PyESPCar色块追踪简易说明文档
2018-10-08 更新examples例程配图
2018-10-09 修改了一个sdk的bug
2018-10-09 添加了两个doc 状态机主题(历史)
2018-10-12 添加开发环境配置文档
2018-10-12 修改doc的url
2018-10-12 添加文档配图
2018-10-12 添加PyESPCar色块追踪的文档
2018-10-12 更新pyespcar的文档
    [小车硬件材料清单.xlsx]
2018-10-12 修改git clone部分
2018-10-13 安装配置添加paho-mqtt的补丁
2018-10-13 将pip3改成了anaonda
2018-10-13 添加Anaconda镜像
2018-10-13 教程改回pip3安装
2018-10-13 添加环境配置的教程, 把opencv改为从源码编译
2018-10-13 配置教程统一采用pip3
2018-10-14 doc里面添加虚拟机网络桥接
2018-10-15 精简main.py
